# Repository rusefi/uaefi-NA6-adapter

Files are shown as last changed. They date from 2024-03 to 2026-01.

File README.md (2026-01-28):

# uaefi-NA6-adapter

🔴Community support ONLY 🔴

🟢 https://www.shop.rusefi.com/shop/p/uaefi-adapter-for-na6-definitely-has-issues-please-know-what-you-are-doing 🟢

To be used with https://github.com/rusefi/uaefi

powerted by [rusEFI firmware](https://github.com/rusefi/rusefi)

## fun fact

See https://wiki.rusefi.com/Miata/#mazda-miata for (legacy?) open source Plug and plays

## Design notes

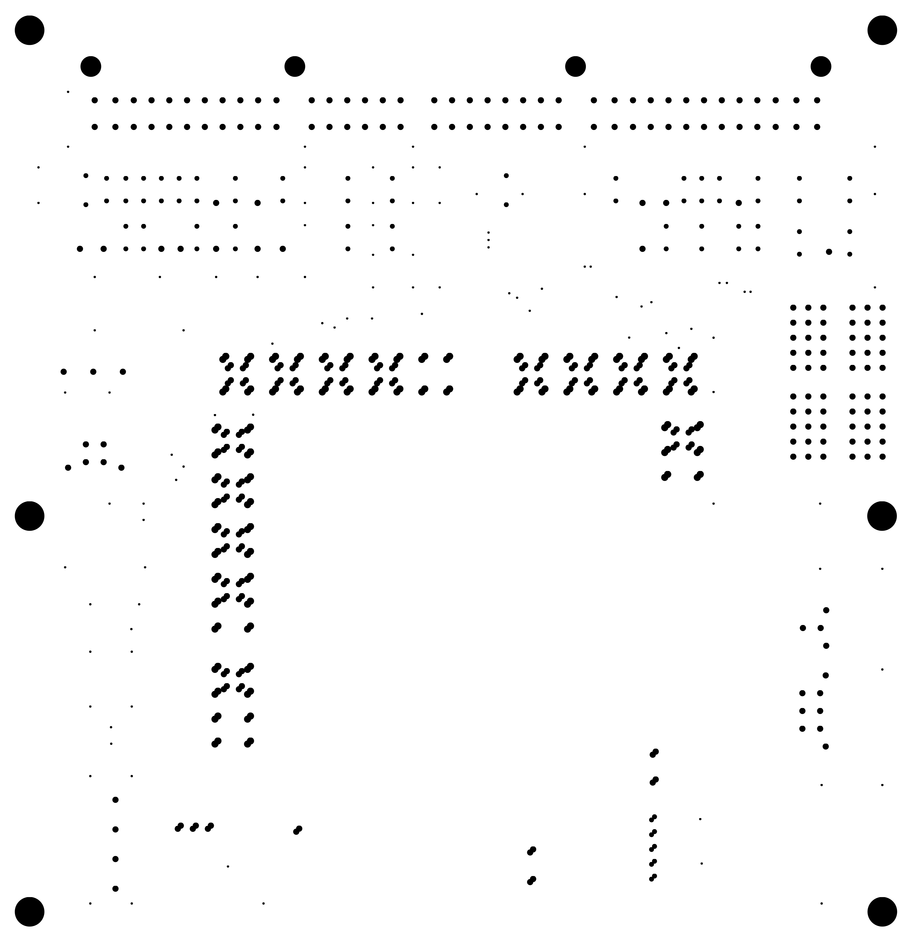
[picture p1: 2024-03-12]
boards/uaefi-adapter-NA-90-95-a/board/misc/uaefi-adapter-NA-90-95-a-outline.png

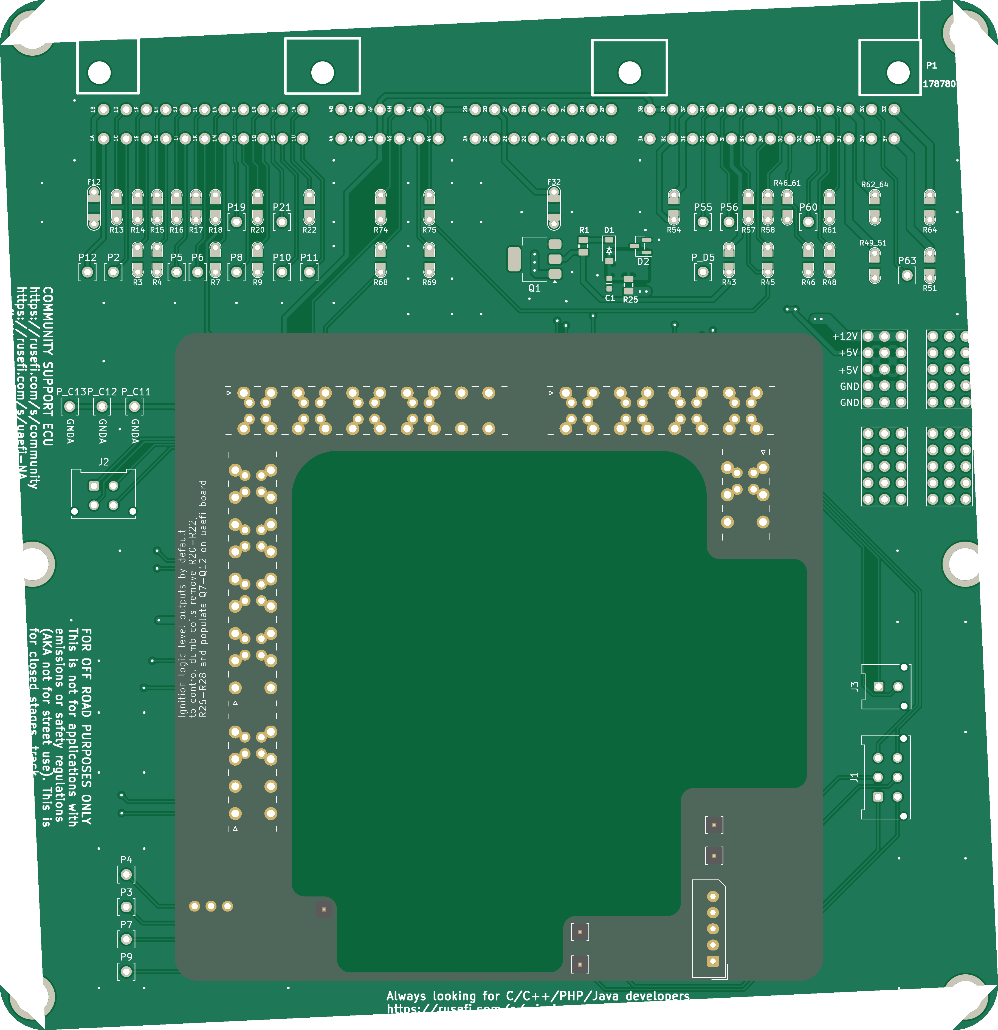
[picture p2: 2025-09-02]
boards/uaefi-adapter-NA-90-95-b/board/uaefi-adapter-NA-90-95-b.png

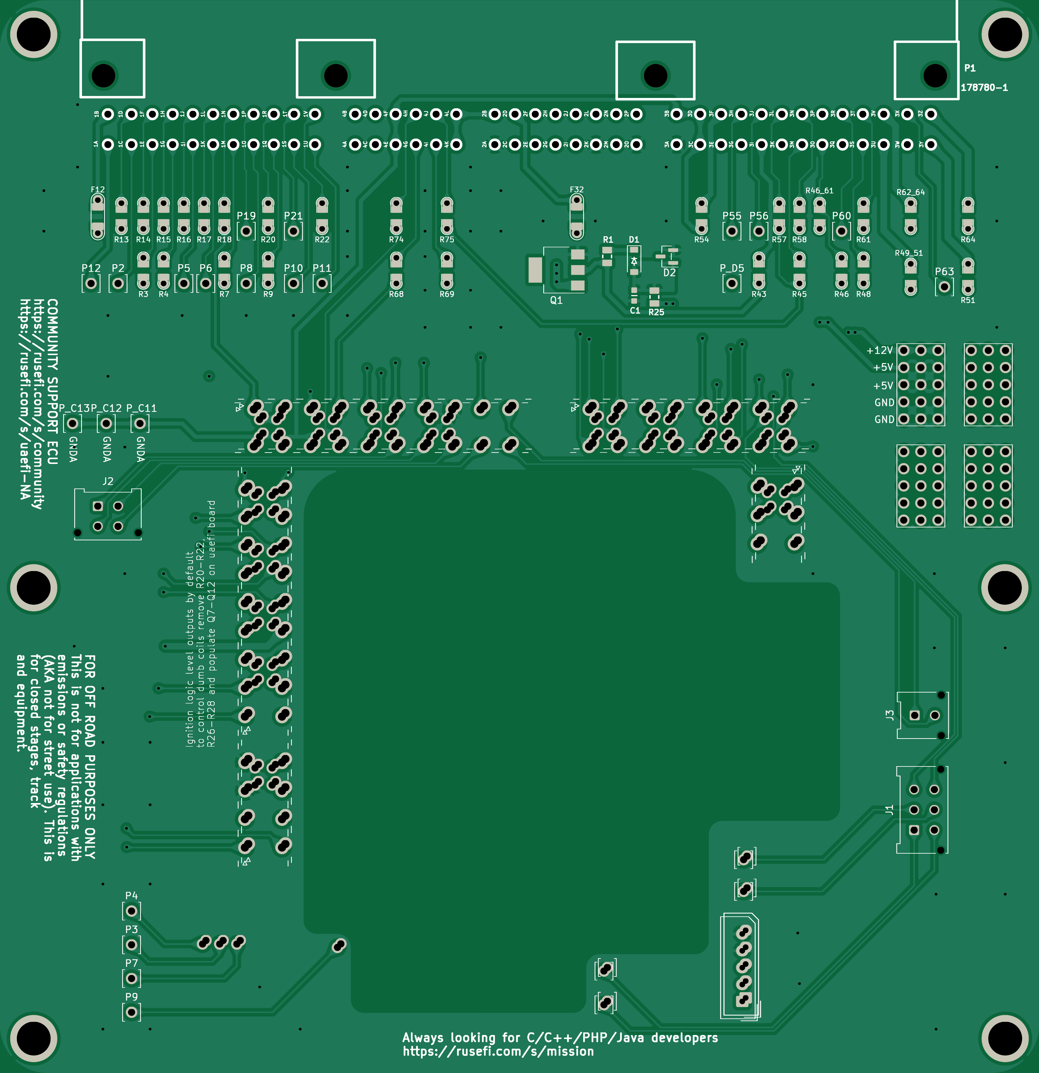
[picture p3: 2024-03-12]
boards/uaefi-adapter-NA-90-95-a/board/misc/uaefi-adapter-NA-90-95-a-top.png

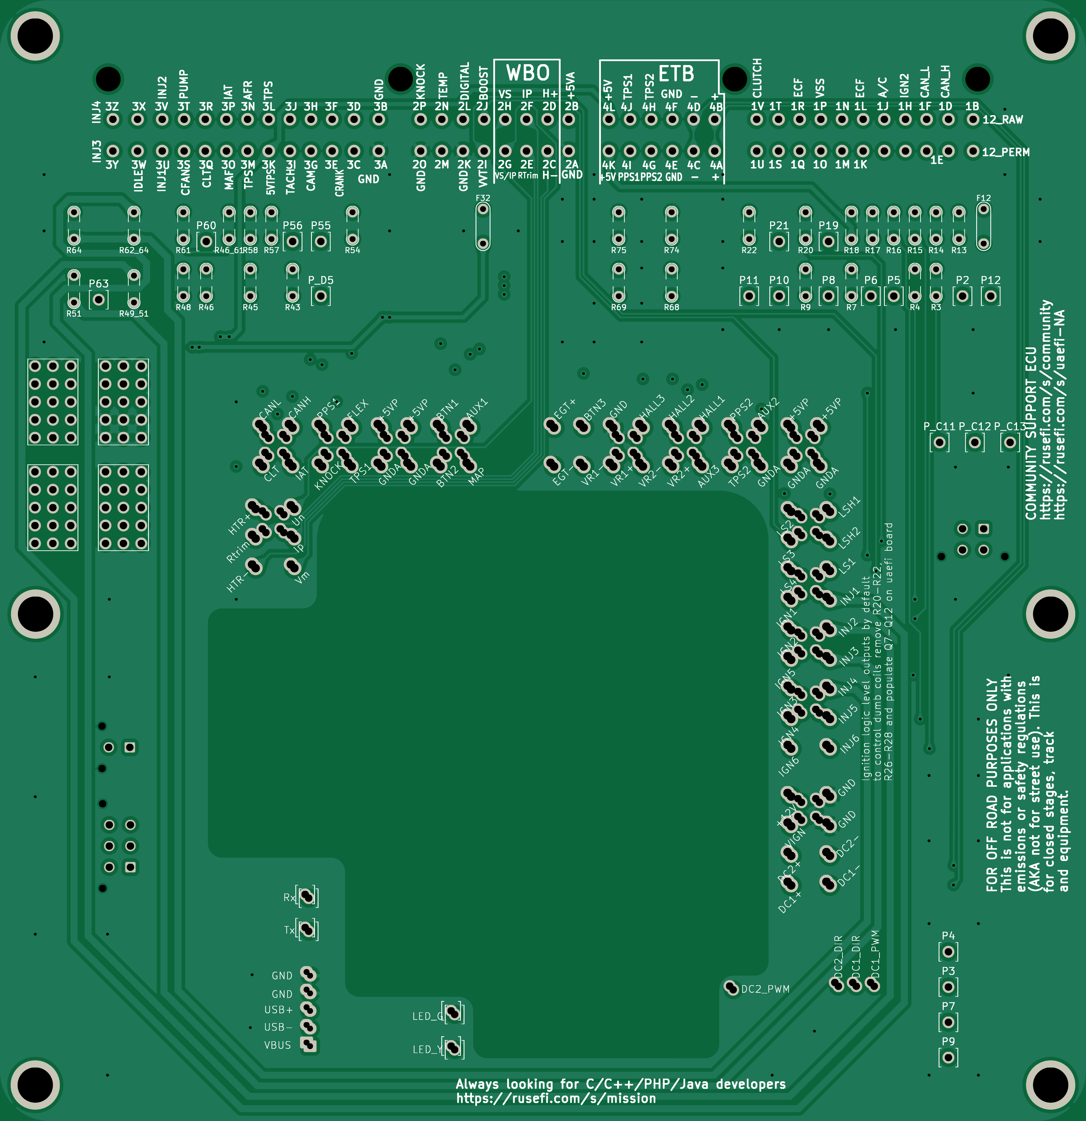
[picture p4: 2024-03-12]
boards/uaefi-adapter-NA-90-95-a/board/misc/uaefi-adapter-NA-90-95-a-bottom.png

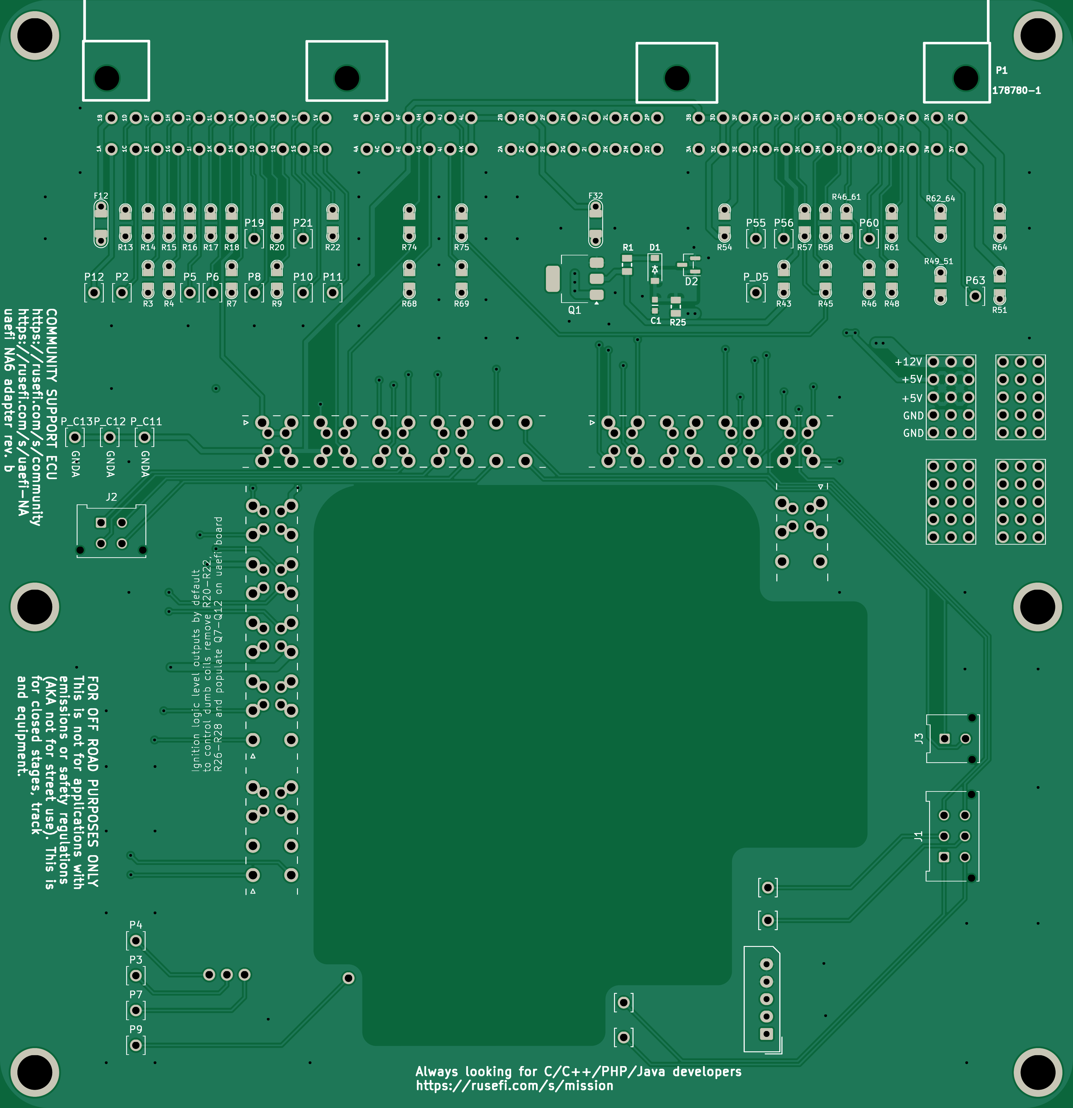
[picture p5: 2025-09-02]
boards/uaefi-adapter-NA-90-95-b/board/misc/uaefi-adapter-NA-90-95-b-top.png

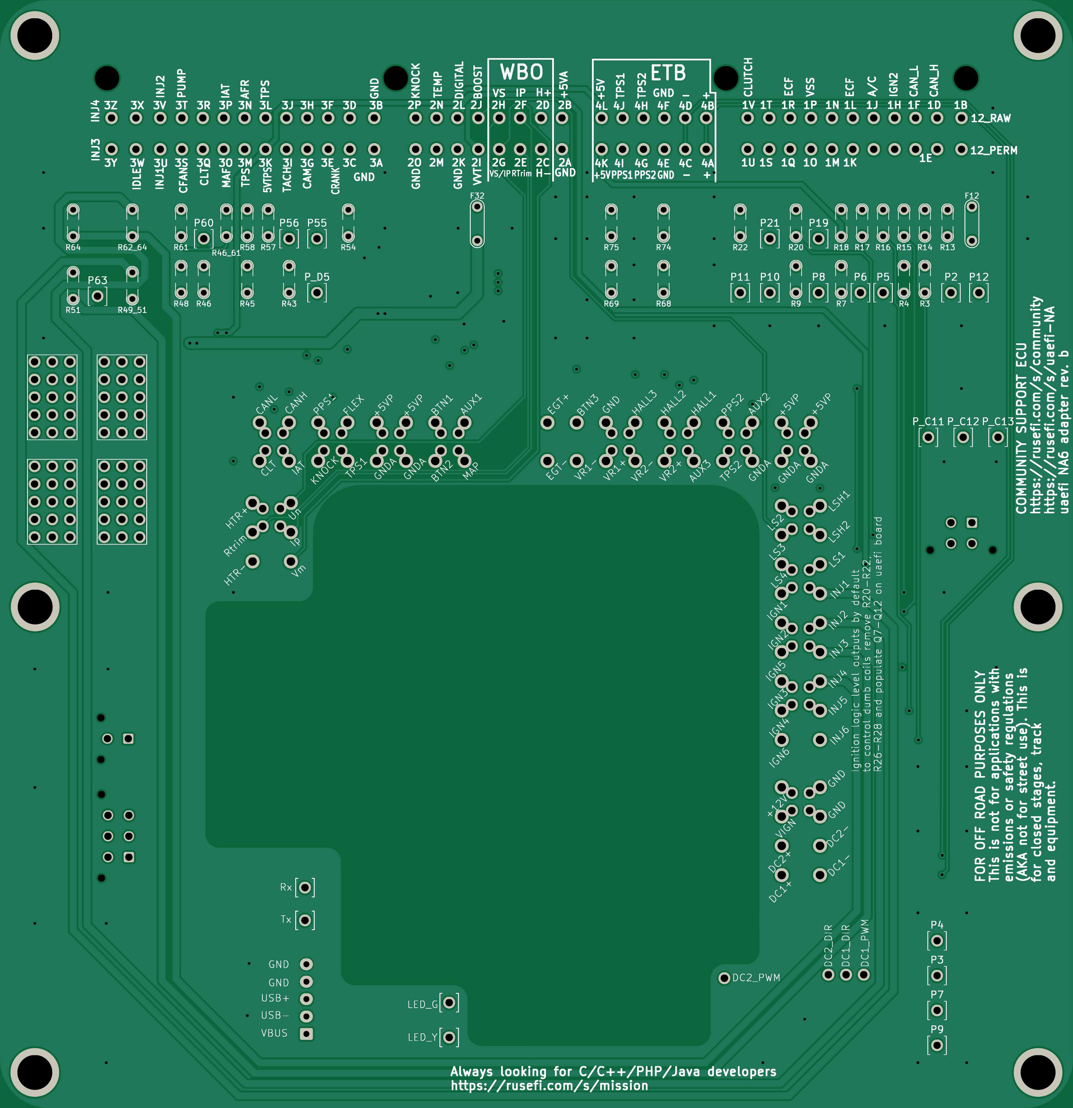
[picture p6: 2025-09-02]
boards/uaefi-adapter-NA-90-95-b/board/misc/uaefi-adapter-NA-90-95-b-bottom.png

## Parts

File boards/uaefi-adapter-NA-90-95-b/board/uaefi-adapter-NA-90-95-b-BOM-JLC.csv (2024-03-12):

Comment | Designator | Footprint | LCSC Part #
100n | C1 | C0603 | C14663
B5819W | D1 | SOD-123 | C8598
PSM712-LF | D2 | SOT-23 | C32677
Fuse-Pad-Pad | F12, F32 | PAD-1206-PAD | C182446
43045-0212 | J3 | Molex_Micro-Fit_3.0_43045-0212_2x01_P3.00mm_Vertical | C293362
ZXMS6005SGTA | Q1 | SOT-223 | C174042
750 | R1 | R0805 | C17818
Jumper-Pad-Pad | R3, R4, R7, R9, R13, R14, R15, R16, R17, R18, R20, R22, R43, R45, R46, R46_61, R48, R49_51, R51, R54, R57, R58, R61, R62_64, R64, R68, R69, R74, R75 | PAD-0805-PAD | C17477
220 | R25 | R0805 | C17557
Conn_01x05_Pin | J801 | Molex_SPOX_5267-05A_1x05_P2.50mm_Vertical | C492404
Conn_01x03_Pin | J802 | 1x3_2.54 | C49257
Conn_02x02_Odd_Even | J803, J804, J805, J806, J807, J808, J809, J810, J811, J812, J813, J814, J815, J816 | 2x2_2.54 | C492419
Conn_01x01_Pin | P801, P802, P803, P804, P805 | 1x1 | C81276

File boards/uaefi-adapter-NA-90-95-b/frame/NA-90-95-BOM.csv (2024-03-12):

Comment | Designator | Footprint | LCSC Part #
100n | C1 | C0603 | C14663
B5819W | D1 | SOD-123 | C8598
PSM712-LF | D2 | SOT-23 | C32677
Fuse-Pad-Pad | F12 | PAD-1206-PAD | C182446
Fuse-Pad-Pad | F32 | PAD-1206-PAD | C182446
PROTO_AREA | G8 | PROTO_AREA
PROTO_AREA | G9 | PROTO_AREA
PROTO_AREA | G10 | PROTO_AREA
PROTO_AREA | G11 | PROTO_AREA
43045-0612 | J1 | Molex_Micro-Fit_3.0_43045-0612_2x03_P3.00mm_Vertical
43045-0412 | J2 | Molex_Micro-Fit_3.0_43045-0412_2x02_P3.00mm_Vertical
43045-0212 | J3 | Molex_Micro-Fit_3.0_43045-0212_2x01_P3.00mm_Vertical | C293362
Module:uaefi/0.2 | M1 | uaefi
178780-1 | P1 | 178780-1_OBD1
Pad | P2 | PAD-TH
Pad | P3 | PAD-TH
Pad | P4 | PAD-TH
Pad | P5 | PAD-TH
Pad | P6 | PAD-TH
Pad | P7 | PAD-TH
Pad | P8 | PAD-TH
Pad | P9 | PAD-TH
Pad | P10 | PAD-TH
Pad | P11 | PAD-TH
Pad | P12 | PAD-TH
Pad | P19 | PAD-TH
Pad | P21 | PAD-TH
Pad | P55 | PAD-TH
Pad | P56 | PAD-TH
Pad | P60 | PAD-TH
Pad | P63 | PAD-TH
Pad | P_C11 | PAD-TH
Pad | P_C12 | PAD-TH
Pad | P_C13 | PAD-TH
Pad | P_D5 | PAD-TH
ZXMS6005SGTA | Q1 | SOT-223 | C174042
750 | R1 | R0805 | C17818
Jumper-Pad-Pad | R3 | PAD-0805-PAD | C17477
Jumper-Pad-Pad | R4 | PAD-0805-PAD | C17477
Jumper-Pad-Pad | R7 | PAD-0805-PAD | C17477
Jumper-Pad-Pad | R9 | PAD-0805-PAD | C17477
Jumper-Pad-Pad | R13 | PAD-0805-PAD | C17477
Jumper-Pad-Pad | R14 | PAD-0805-PAD | C17477
Jumper-Pad-Pad | R15 | PAD-0805-PAD | C17477
Jumper-Pad-Pad | R16 | PAD-0805-PAD | C17477
Jumper-Pad-Pad | R17 | PAD-0805-PAD | C17477
Jumper-Pad-Pad | R18 | PAD-0805-PAD | C17477
Jumper-Pad-Pad | R20 | PAD-0805-PAD | C17477
Jumper-Pad-Pad | R22 | PAD-0805-PAD | C17477
220 | R25 | R0805 | C17557
Jumper-Pad-Pad | R43 | PAD-0805-PAD | C17477
Jumper-Pad-Pad | R45 | PAD-0805-PAD | C17477
Jumper-Pad-Pad | R46 | PAD-0805-PAD | C17477
Jumper-Pad-Pad | R46_61 | PAD-0805-PAD | C17477
Jumper-Pad-Pad | R48 | PAD-0805-PAD | C17477
Jumper-Pad-Pad | R49_51 | PAD-0805-PAD | C17477
Jumper-Pad-Pad | R51 | PAD-0805-PAD | C17477
Jumper-Pad-Pad | R54 | PAD-0805-PAD | C17477
Jumper-Pad-Pad | R57 | PAD-0805-PAD | C17477
Jumper-Pad-Pad | R58 | PAD-0805-PAD | C17477
Jumper-Pad-Pad | R61 | PAD-0805-PAD | C17477
Jumper-Pad-Pad | R62_64 | PAD-0805-PAD | C17477
Jumper-Pad-Pad | R64 | PAD-0805-PAD | C17477
Jumper-Pad-Pad | R68 | PAD-0805-PAD | C17477
Jumper-Pad-Pad | R69 | PAD-0805-PAD | C17477
Jumper-Pad-Pad | R74 | PAD-0805-PAD | C17477
Jumper-Pad-Pad | R75 | PAD-0805-PAD | C17477

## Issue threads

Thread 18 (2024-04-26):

a few traces are too thin

rusefillc, 2024-04-26:
We suspect that on unmarked rev A the following traces are too narrow:

* IDLE
* WBO heater
* VVT
* maybe something else?

Closed 2025-09-02.

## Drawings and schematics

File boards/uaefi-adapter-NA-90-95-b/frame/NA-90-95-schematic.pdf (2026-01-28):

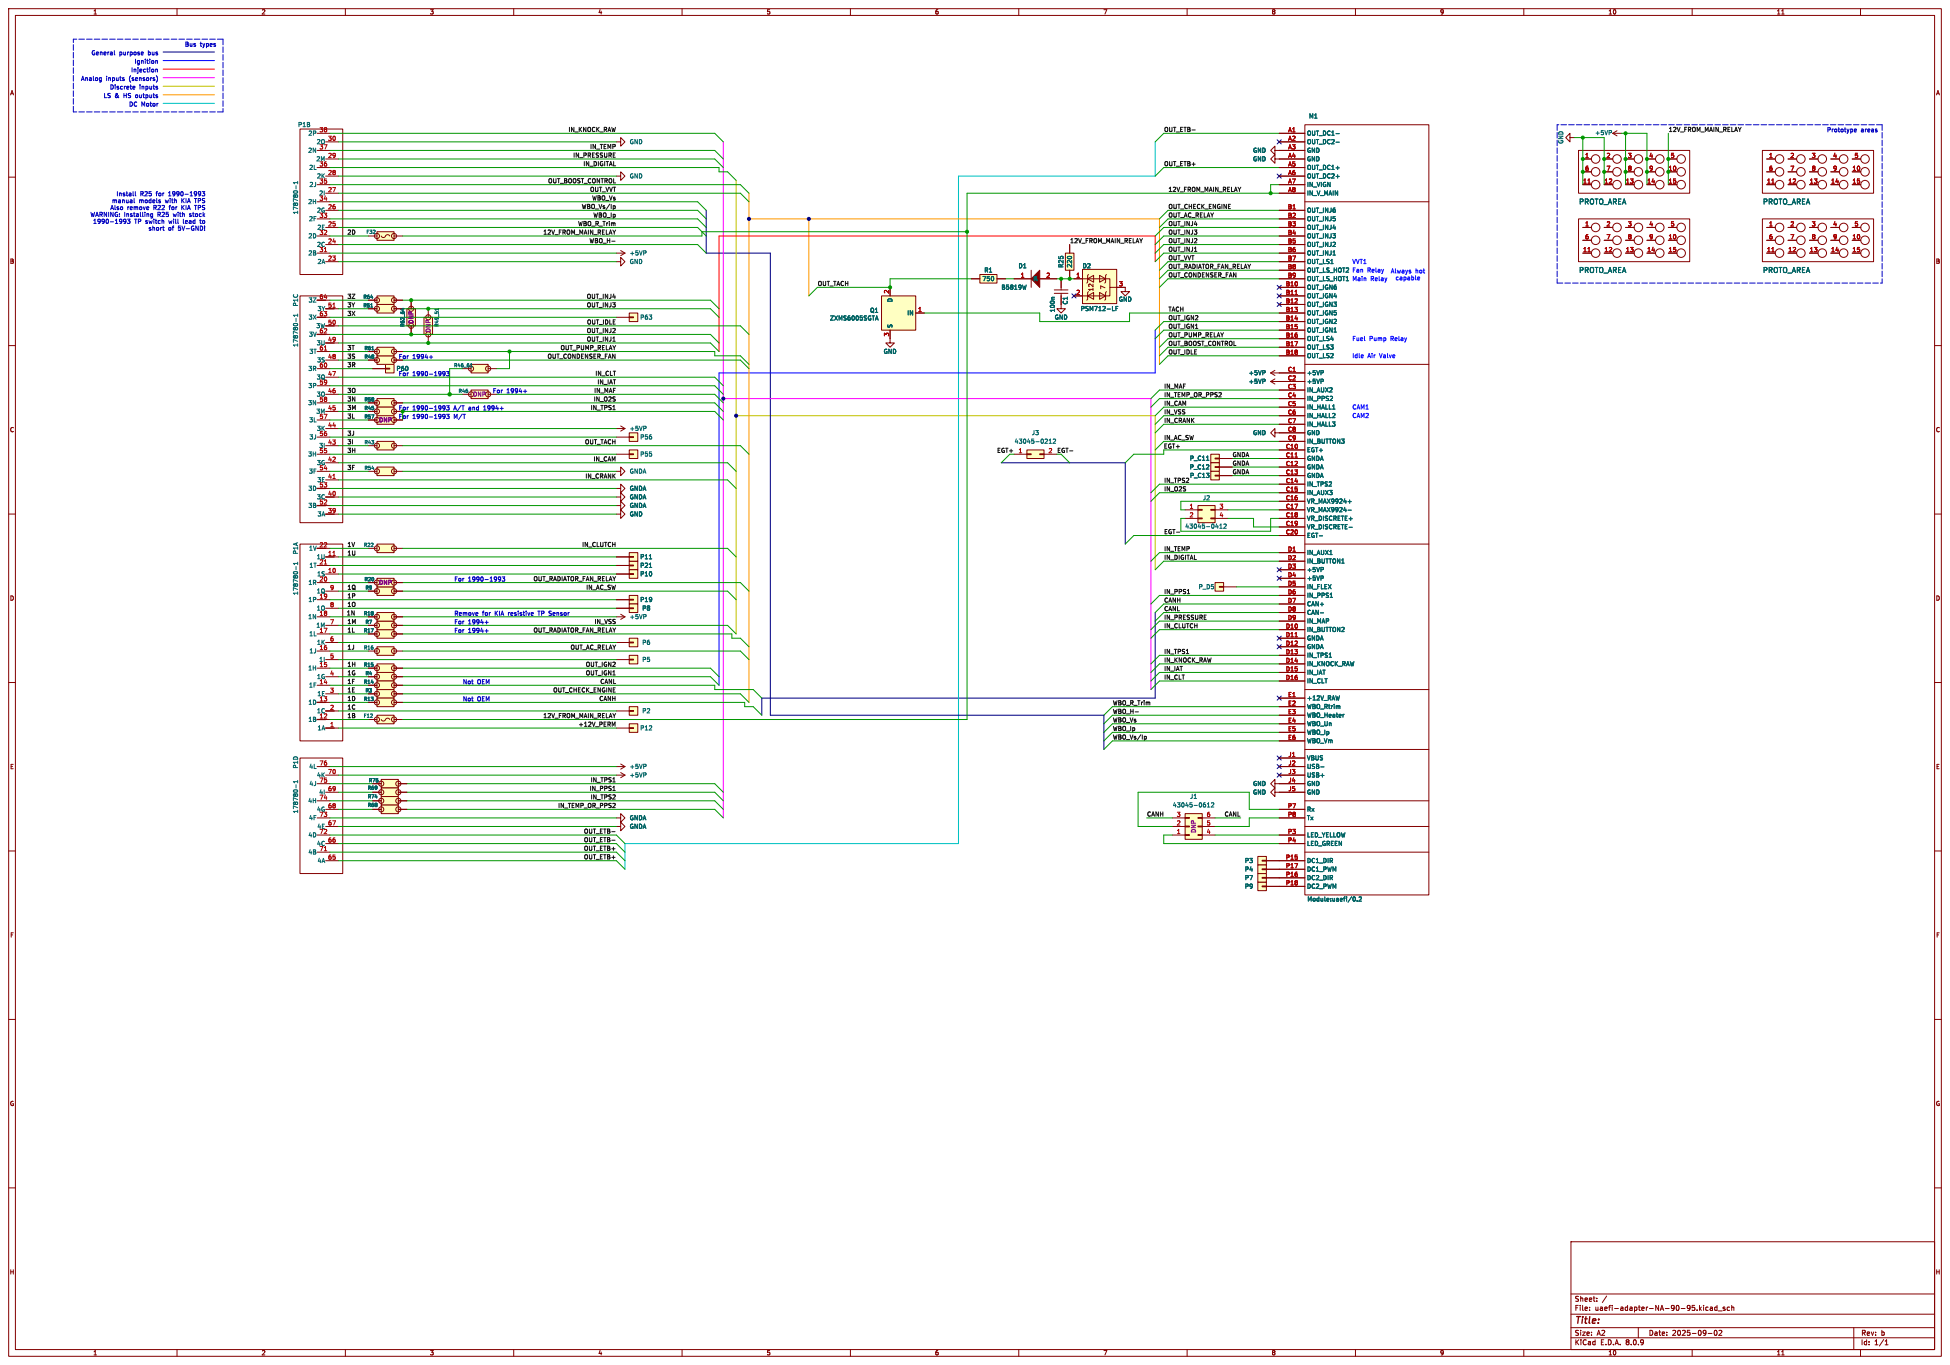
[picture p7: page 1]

Discrete inputs General purpose bus LS & HS outputs

short of 5V-GND! DC Motor

IN_VIGN
Idle Air Valve Main Relay VVT1
capable CAM1 CAM2 Fan Relay Fuel Pump Relay

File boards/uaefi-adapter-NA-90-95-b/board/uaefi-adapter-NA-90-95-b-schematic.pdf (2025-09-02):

# Idle Air Valve Main Relay VVT1

A8 | OUT_INJ6 B1 | OUT_IGN6 B10 | OUT_IGN4 B11 | OUT_IGN3 B12 | OUT_IGN5 B13 | OUT_IGN2 B14 | OUT_IGN1 B15 | OUT_LS4 B16 | OUT_LS3 B17 | OUT_LS2 B18 | OUT_INJ5 B2 | OUT_INJ4 B3 | OUT_INJ3 B4 | OUT_INJ2 B5 | OUT_INJ1 B6 | OUT_LS1 B7 | OUT_LS_HOT2 B8 | OUT_LS_HOT1 B9 | +5VP C1 | EGT+ C10 | GNDA C11 | GNDA C12 | GNDA C13


Discrete inputs General purpose bus LS & HS outputs

short of 5V-GND! DC Motor

capable CAM1 CAM2 Fan Relay Fuel Pump Relay

J811 1 | 2 3 | 4

# Idle Air Valve Main Relay VVT1

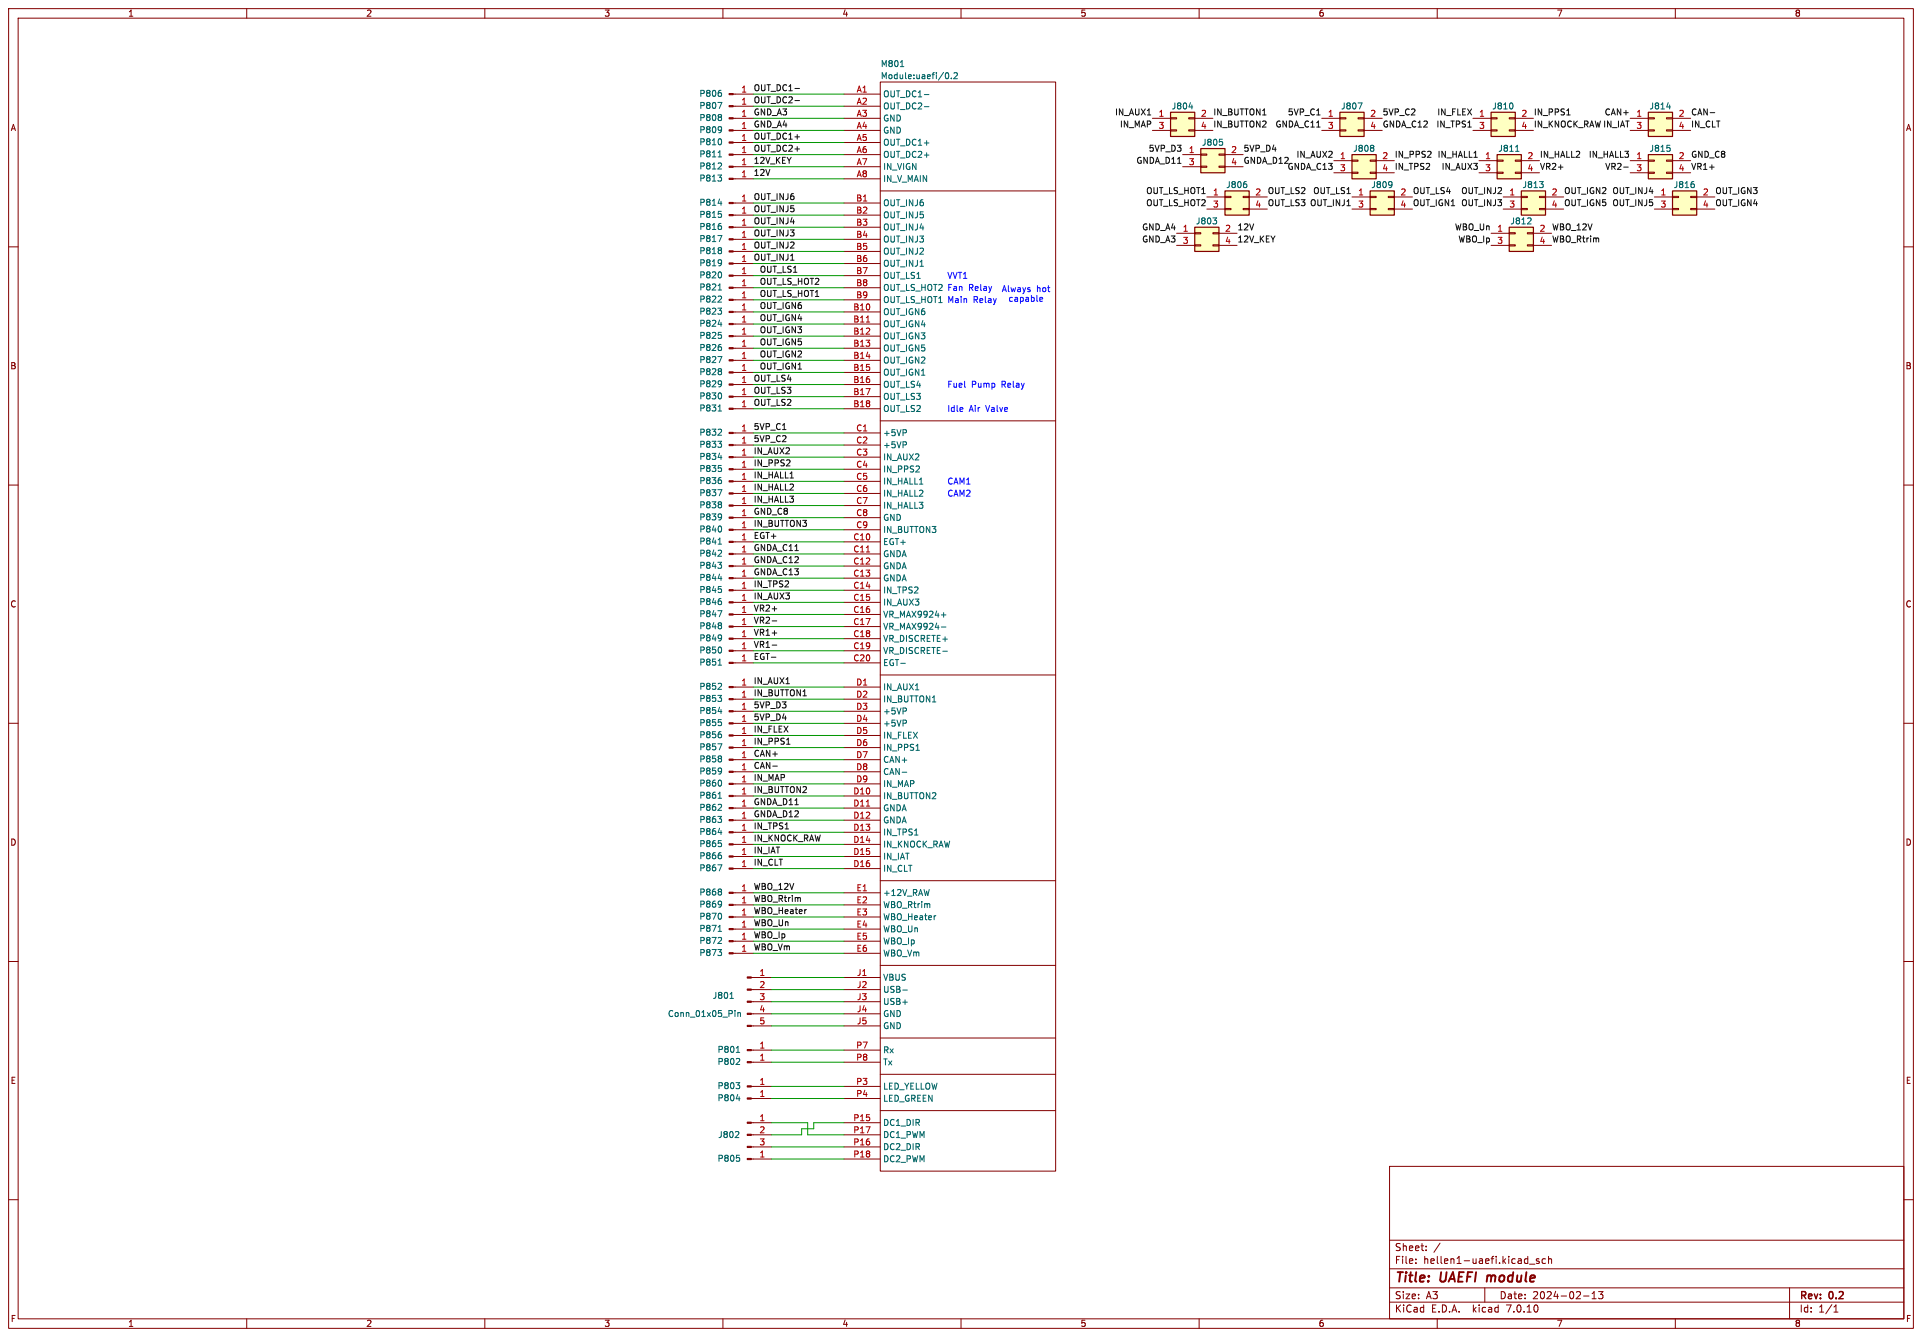
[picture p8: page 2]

capable CAM1 CAM2 Fan Relay Fuel Pump Relay

Id: 1/1 Title: UAEFI module

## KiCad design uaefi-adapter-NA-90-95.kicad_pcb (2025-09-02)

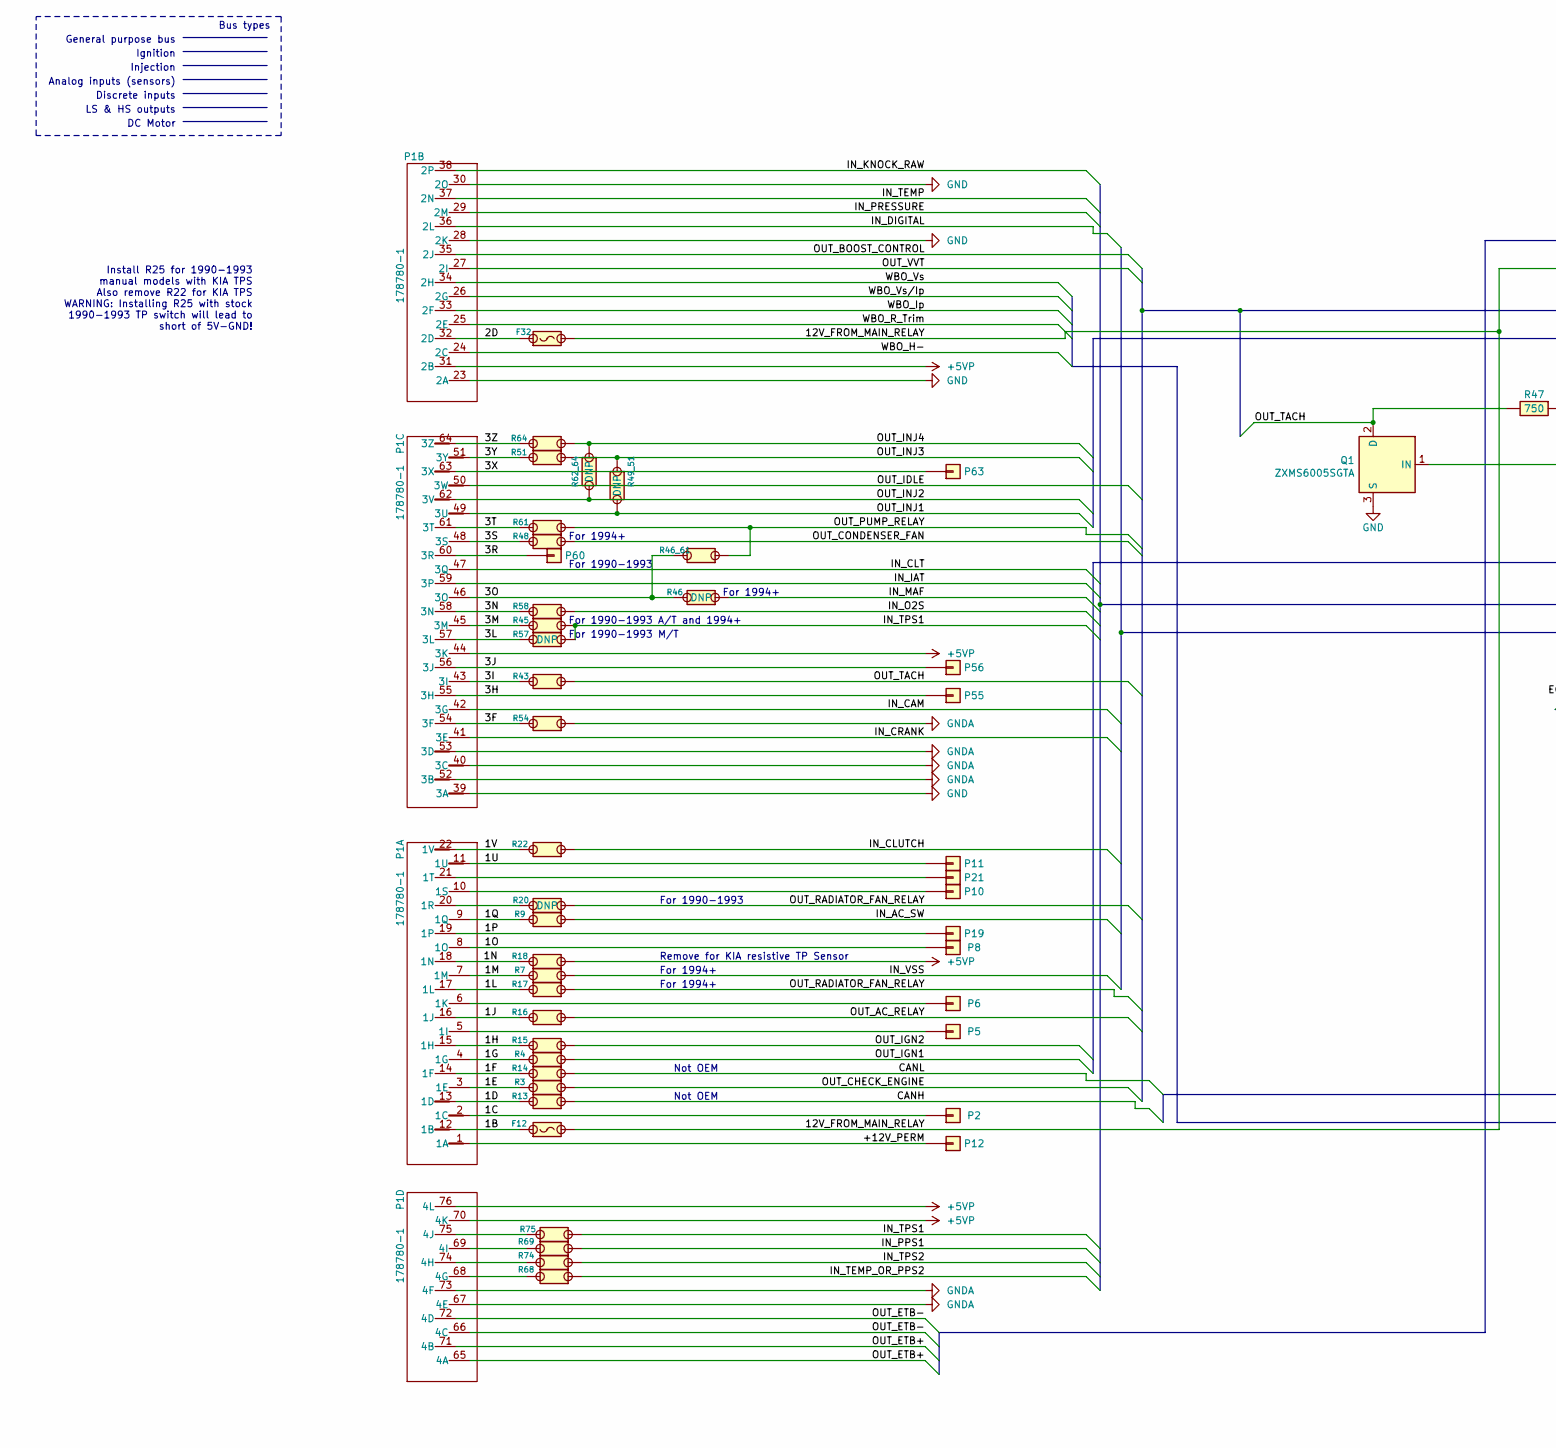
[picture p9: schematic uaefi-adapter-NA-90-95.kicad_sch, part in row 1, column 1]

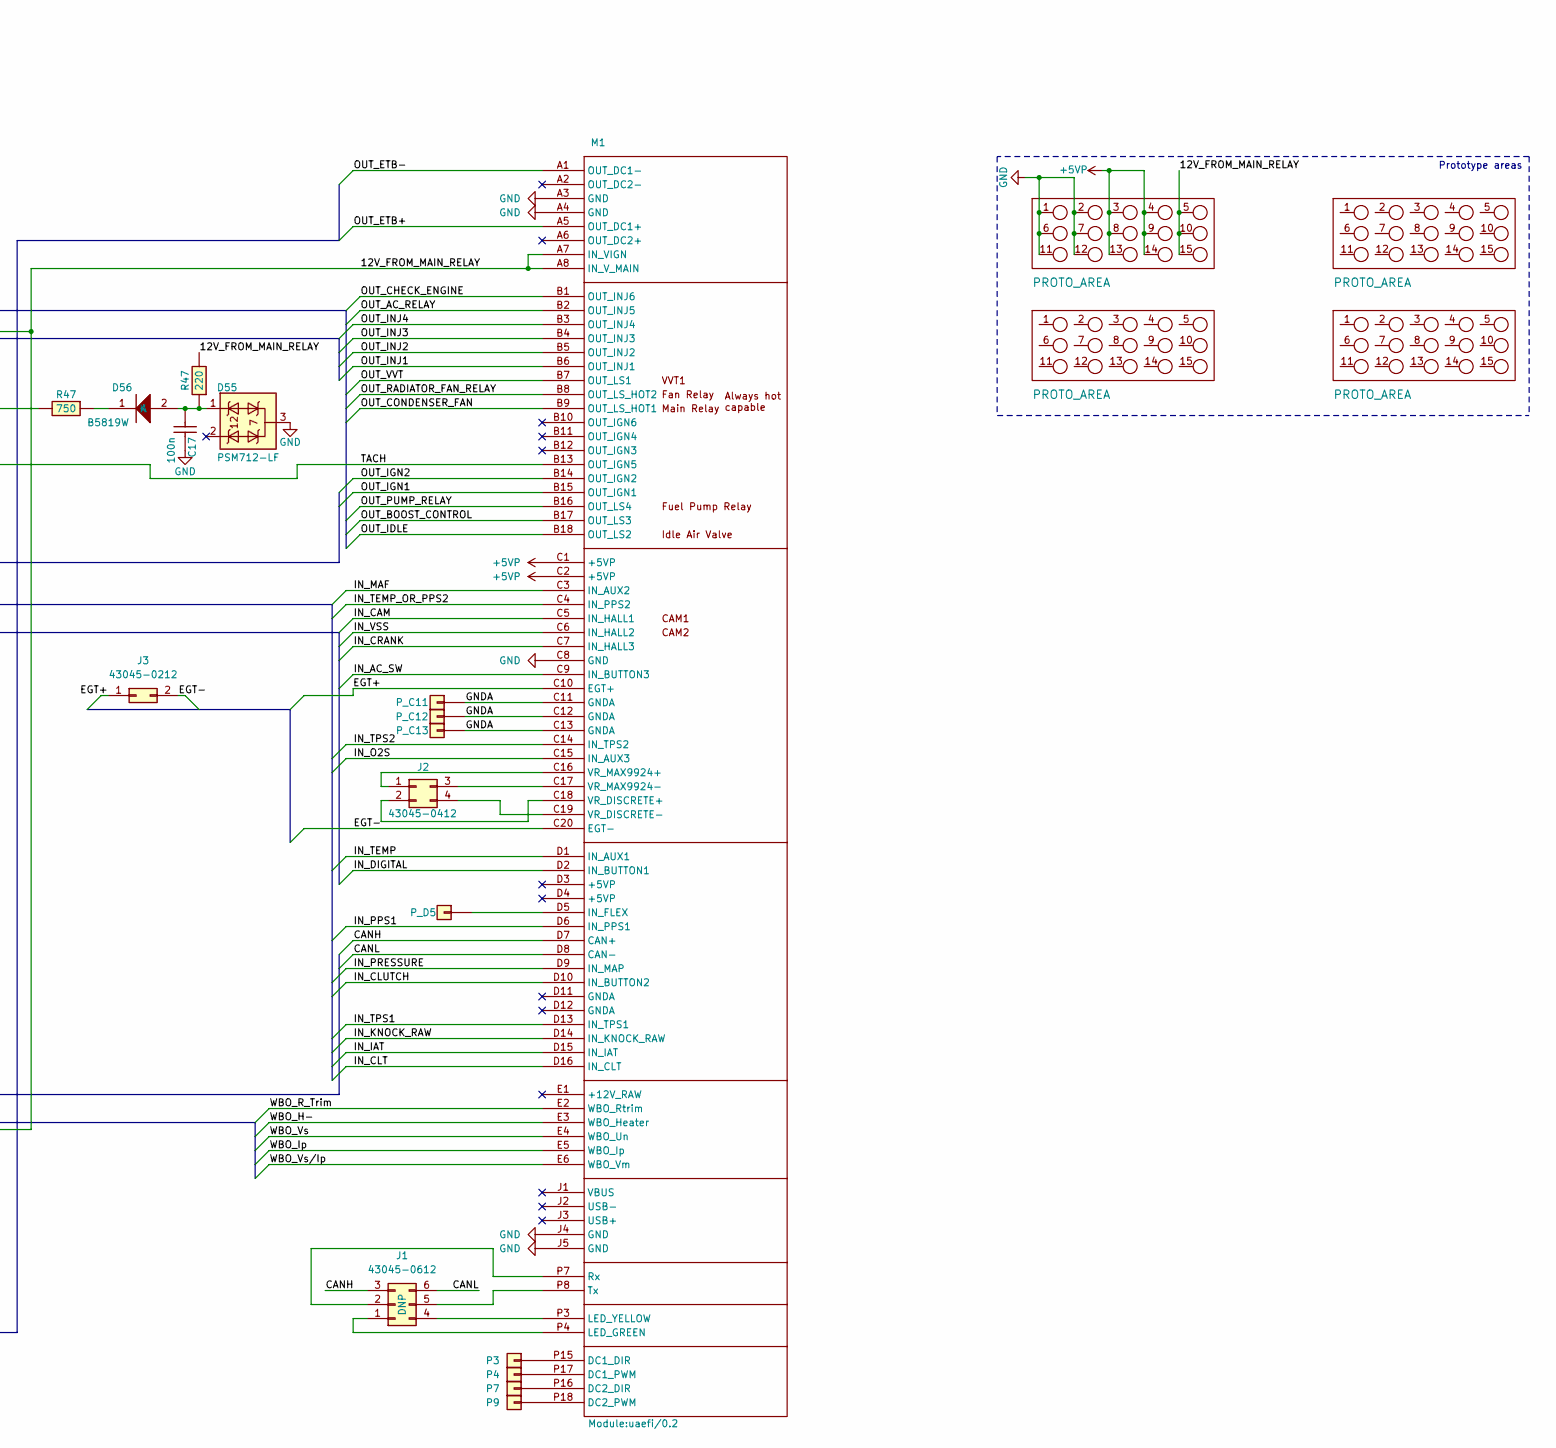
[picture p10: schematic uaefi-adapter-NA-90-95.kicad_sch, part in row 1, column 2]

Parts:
C17: 100n; C0603; LCSC C14663
D55: PSM712-LF; SOT-23; LCSC C32677
D56: B5819W; SOD-123; LCSC C8598
F12, F32: Fuse-Pad-Pad; PAD-1206-PAD; LCSC C182446
G8, G9, G10, G11: PROTO_AREA
J1: 43045-0612; Molex_Micro-Fit_3.0_43045-0612_2x03_P3.00mm_Vertical
J2: 43045-0412; Molex_Micro-Fit_3.0_43045-0412_2x02_P3.00mm_Vertical
J3: 43045-0212; Molex_Micro-Fit_3.0_43045-0212_2x01_P3.00mm_Vertical; LCSC C293362
M1: Module:uaefi/0.2; uaefi
P1: 178780-1; 178780-1_OBD1
P2, P3, P4, P5, P6, P7, P8, P9, P10, P11, P12, P19, P21, P55, P56, P60, P63: Pad; PAD-TH
P_C11, P_C12, P_C13: Pad; PAD-TH
P_D5: Pad; PAD-TH
Q1: ZXMS6005SGTA; SOT-223; LCSC C174042
R3, R4, R7, R9, R13, R14, R15, R16, R17, R18, R22, R43, R45, R46_61, R48, R51, R54, R58, R61, R64, R68, R69, R74, R75: Jumper-Pad-Pad; PAD-0805-PAD; LCSC C17477
R20, R46, R49_51, R57, R62_64: Jumper-Pad-Pad; PAD-0805-PAD
R47: 220; R0805; LCSC C17557

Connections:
+5VP: G8.3, G8.4, G8.8, G8.9, G8.13, G8.14, M1.C1 (+5VP), M1.C2 (+5VP), P1.31 (2B), P1.44 (3K), P1.70 (4K), P1.76 (4L), R18.1
/1B: F12.1, P1.12 (1B)
/1C: P1.2 (1C), P2.1
/1D: P1.13 (1D), R13.2
/1E: P1.3 (1E), R3.2
/1F: P1.14 (1F), R14.2
/1G: P1.4 (1G), R4.2
/1H: P1.15 (1H), R15.2
/1J: P1.16 (1J), R16.2
/1L: P1.17 (1L), R17.2
/1M: P1.7 (1M), R7.2
/1N: P1.18 (1N), R18.2
/1O: P1.8 (1O), P8.1
/1P: P1.19 (1P), P19.1
/1Q: P1.9 (1Q), R9.2
/1U: P1.11 (1U), P11.1
/1V: P1.22 (1V), R22.2
/2D: F32.1, P1.32 (2D)
/3F: P1.54 (3F), R54.2
/3H: P1.55 (3H), P55.1
/3I: P1.43 (3I), R43.2
/3J: P1.56 (3J), P56.1
/3L: P1.57 (3L), R57.2
/3M: P1.45 (3M), R45.2
/3N: P1.58 (3N), R58.2
/3O: P1.46 (3O), R46.2, R46_61.2
/3R: P1.60 (3R), P60.1
/3S: P1.48 (3S), R48.2
/3T: P1.61 (3T), R61.2
/3X: P1.63 (3X), P63.1
/3Y: P1.51 (3Y), R51.2
/3Z: P1.64 (3Z), R64.2
/12V_FROM_MAIN_RELAY: F12.2, F32.2, G8.5, G8.10, G8.15, M1.A7 (IN_VIGN), M1.A8 (IN_V_MAIN); also elsewhere on the board
/+12V_PERM: P1.1 (1A), P12.1
/CANH: J1.3, M1.D7 (CAN+), R13.1
/CANL: J1.6, M1.D8 (CAN-), R14.1
/EGT+: J3.1, M1.C10 (EGT+)
/EGT-: J3.2, M1.C20 (EGT-)
/IN_AC_SW: M1.C9 (IN_BUTTON3), R9.1
/IN_CAM: M1.C5 (IN_HALL1), P1.42 (3G)
/IN_CLT: M1.D16 (IN_CLT), P1.47 (3Q)
/IN_CLUTCH: M1.D10 (IN_BUTTON2), R22.1
/IN_CRANK: M1.C7 (IN_HALL3), P1.41 (3E)
/IN_DIGITAL: M1.D2 (IN_BUTTON1), P1.36 (2L)
/IN_IAT: M1.D15 (IN_IAT), P1.59 (3P)
/IN_KNOCK_RAW: M1.D14 (IN_KNOCK_RAW), P1.38 (2P)
/IN_MAF: M1.C3 (IN_AUX2), R46.1
/IN_O2S: M1.C15 (IN_AUX3), R58.1
/IN_PPS1: M1.D6 (IN_PPS1), R69.1
/IN_PRESSURE: M1.D9 (IN_MAP), P1.29 (2M)
/IN_TEMP: M1.D1 (IN_AUX1), P1.37 (2N)
/IN_TEMP_OR_PPS2: M1.C4 (IN_PPS2), R68.1
/IN_TPS1: M1.D13 (IN_TPS1), R45.1, R57.1, R75.1
/IN_TPS2: M1.C14 (IN_TPS2), R74.1
/IN_VSS: M1.C6 (IN_HALL2), R7.1
/OUT_AC_RELAY: M1.B2 (OUT_INJ5), R16.1
/OUT_BOOST_CONTROL: M1.B17 (OUT_LS3), P1.35 (2J)
/OUT_CHECK_ENGINE: M1.B1 (OUT_INJ6), R3.1
/OUT_CONDENSER_FAN: M1.B9 (OUT_LS_HOT1), R48.1
/OUT_ETB+: M1.A5 (OUT_DC1+), P1.65 (4A), P1.71 (4B)
/OUT_ETB-: M1.A1 (OUT_DC1-), P1.66 (4C), P1.72 (4D)
/OUT_IDLE: M1.B18 (OUT_LS2), P1.50 (3W)
/OUT_IGN1: M1.B15 (OUT_IGN1), R4.1
/OUT_IGN2: M1.B14 (OUT_IGN2), R15.1
/OUT_INJ1: M1.B6 (OUT_INJ1), P1.49 (3U), R49_51.2
/OUT_INJ2: M1.B5 (OUT_INJ2), P1.62 (3V), R62_64.2
/OUT_INJ3: M1.B4 (OUT_INJ3), R49_51.1, R51.1
/OUT_INJ4: M1.B3 (OUT_INJ4), R62_64.1, R64.1
/OUT_PUMP_RELAY: M1.B16 (OUT_LS4), R46_61.1, R61.1
/OUT_RADIATOR_FAN_RELAY: M1.B8 (OUT_LS_HOT2), R17.1, R20.1
/OUT_TACH: Q1.2 (D), R43.1; also elsewhere on the board
/OUT_VVT: M1.B7 (OUT_LS1), P1.27 (2I)
/TACH: M1.B13 (OUT_IGN5), Q1.1 (IN)
/WBO_H-: M1.E3 (WBO_Heater), P1.24 (2C)
/WBO_Ip: M1.E5 (WBO_Ip), P1.33 (2F)
/WBO_R_Trim: M1.E2 (WBO_Rtrim), P1.25 (2E)
/WBO_Vs: M1.E4 (WBO_Un), P1.34 (2H)
/WBO_Vs/Ip: M1.E6 (WBO_Vm), P1.26 (2G)
GND: G8.1, G8.2, G8.6, G8.7, G8.11, G8.12, M1.A3 (GND), M1.A4 (GND), M1.C8 (GND), M1.J4 (GND), M1.J5 (GND), P1.23 (2A), P1.28 (2K), P1.30 (2O), P1.39 (3A), Q1.3 (S); also elsewhere on the board
GNDA: M1.C11 (GNDA), M1.C12 (GNDA), M1.C13 (GNDA), P1.40 (3C), P1.52 (3B), P1.53 (3D), P1.67 (4E), P1.73 (4F), P_C11.1, P_C12.1, P_C13.1, R54.1
unnamed: J1.1, M1.P4 (LED_GREEN)
unnamed: J1.2, M1.P7 (Rx)
unnamed: J1.4, M1.P3 (LED_YELLOW)
unnamed: J1.5, M1.P8 (Tx)
unnamed: J2.1, M1.C16 (VR_MAX9924+)
unnamed: J2.2, M1.C18 (VR_DISCRETE+)
unnamed: J2.3, M1.C17 (VR_MAX9924-)
unnamed: J2.4, M1.C19 (VR_DISCRETE-)
unnamed: M1.P15 (DC1_DIR), P3.1
unnamed: M1.P17 (DC1_PWM), P4.1
unnamed: M1.P16 (DC2_DIR), P7.1
unnamed: M1.P18 (DC2_PWM), P9.1
unnamed: M1.D5 (IN_FLEX), P_D5.1
unnamed: P1.5 (1I), P5.1
unnamed: P1.6 (1K), P6.1
unnamed: P1.20 (1R), R20.2
unnamed: P1.21 (1T), P21.1
unnamed: P1.68 (4G), R68.2
unnamed: P1.74 (4H), R74.2
unnamed: P1.69 (4I), R69.2
unnamed: P1.75 (4J), R75.2
unnamed: P1.10 (1S), P10.1

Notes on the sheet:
For 1994+
Injection
For 1990-1993
Discrete inputs
Not OEM
General purpose bus
For 1990-1993
Bus types
For 1994+
LS & HS outputs
Install R25 for 1990-1993 manual models with KIA TPS Also remove R22 for KIA TPS WARNING: Installing R25 with stock 1990-1993 TP switch will lead to short of 5V-GND!
For 1990-1993 M/T
For 1990-1993 A/T and 1994+
DC Motor
Prototype areas
Ignition
Remove for KIA resistive TP Sensor
Analog inputs (sensors)

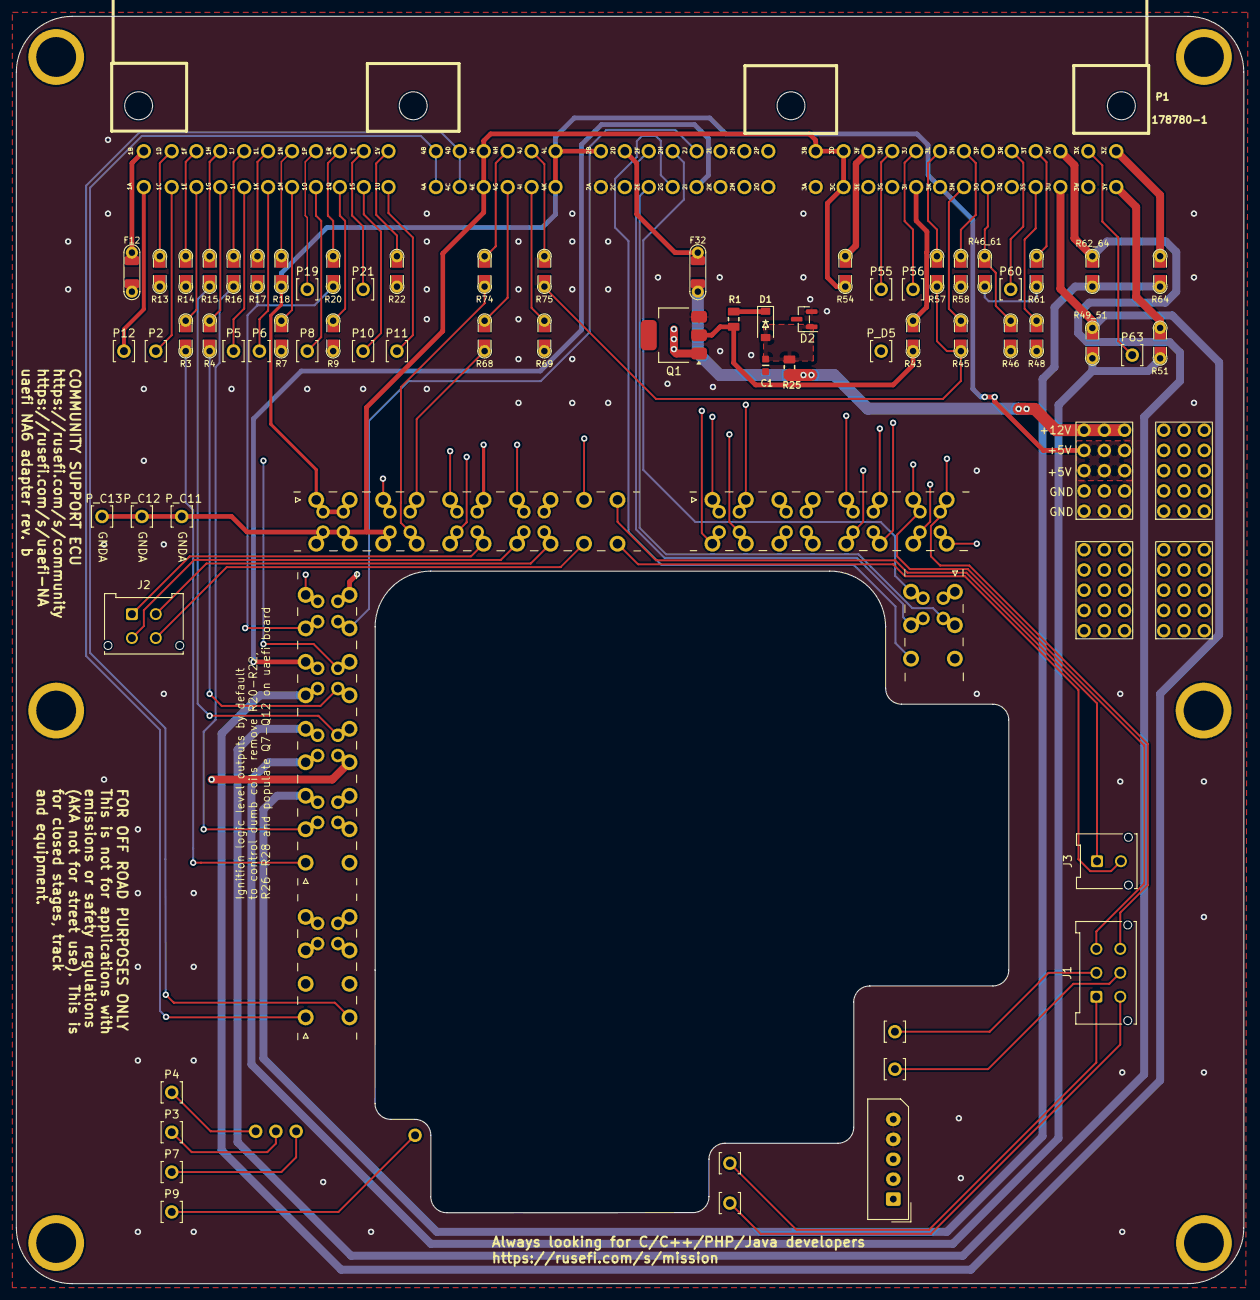
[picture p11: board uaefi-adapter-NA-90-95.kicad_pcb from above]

Board: 4 copper layers, 154.0 x 159.0 mm, 73 parts (0 on the bottom side), 104 nets.

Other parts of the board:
C1: 100n; C0603
D1: B5819W; SOD-123
D2: PSM712-LF; SOT-23
J11, J13, J14, J15, J16, J17: Conn_01x01; MountingHole_4.5mm_Pad
R1: 750; R0805
R25: 220; R0805

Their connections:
/12V_FROM_MAIN_RELAY: R25.2; also elsewhere on the board
/OUT_TACH: R1.2; also elsewhere on the board
GND: C1.1, D2.3; also elsewhere on the board
unnamed: C1.2, D1.2 (A), D2.1, R25.1
unnamed: D1.1 (K), R1.1

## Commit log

2024-02-26 GHA says update kicad6-libraries
2024-03-03 Upd SCH
    [LS4.kicad_sch, uaefi-adapter-NA6.kicad_sch]
2024-03-03 Update kicad6-libraries
2024-03-10 in progress
    [uaefi-adapter-NA-90-95.kicad_pcb]
2024-03-12 [skip actions] Auto-generated board v2.1
    [uaefi-adapter-NA-90-95-B_Cu.gbl, uaefi-adapter-NA-90-95-B_Mask.gbs, uaefi-adapter-NA-90-95-B_Paste.gbp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]
2025-09-02 rev b
    [uaefi-adapter-NA-90-95.kicad_pcb, uaefi-adapter-NA-90-95.kicad_sch]
2025-09-02 #18 #19
    [uaefi-adapter-NA-90-95.kicad_pcb]
